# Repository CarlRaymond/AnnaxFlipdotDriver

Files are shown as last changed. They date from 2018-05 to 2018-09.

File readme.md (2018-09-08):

# Annax Flipdot Driver #

This is a driver for Annax flipdot display panels, with an Arduino nano or ESP8266 (Wemos D1 Mini) controller.

The controller consists of a row driver PC board, which contains the microcontroller,
and a column driver PC board. A span of panels can be any length. One row driver daisy
chains to all the panels, and each panel has its own column driver. The row and column
driver boards are connected together with a serial interface.

The row board acts as the master controller, and holds either an Arduino Nano or a WeMos D1 Mini
module.

The Nano has enough GPIO pins to supprt off-board connections to external controls,
supporting interactive applications. 

The WeMos D1 Mini is an ESP8266 device, with built-in WiFi capability. This allows using
the panel for signage, with remote configuration capability.

## Row Board ##
[Row board schematic](kicad/row_board/pdf/row_driver_schematic.pdf)
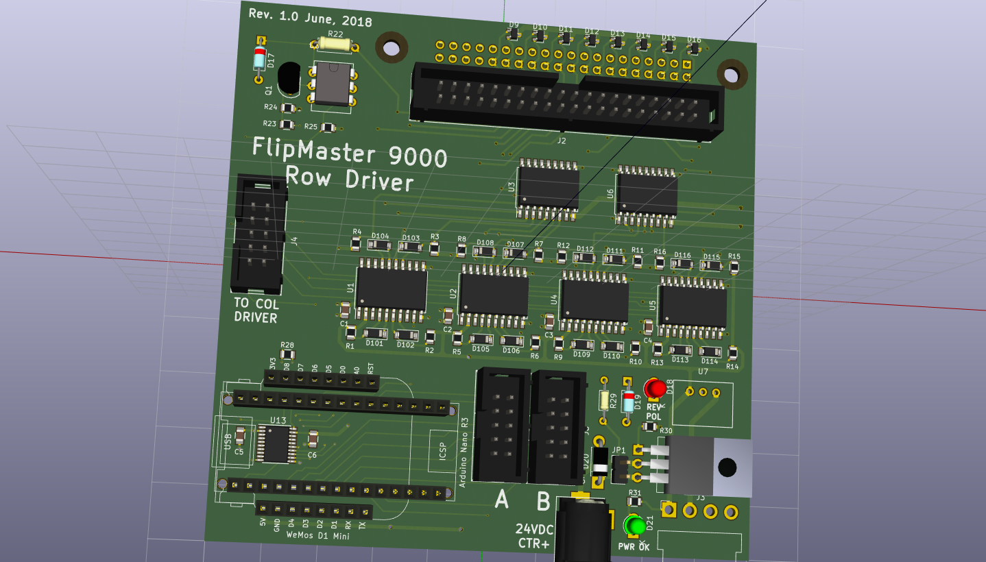
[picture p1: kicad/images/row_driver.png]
Image of row board


## Column Board ##
[Column board schematic](kicad/column_board/pdf/column_driver_schematic.pdf)
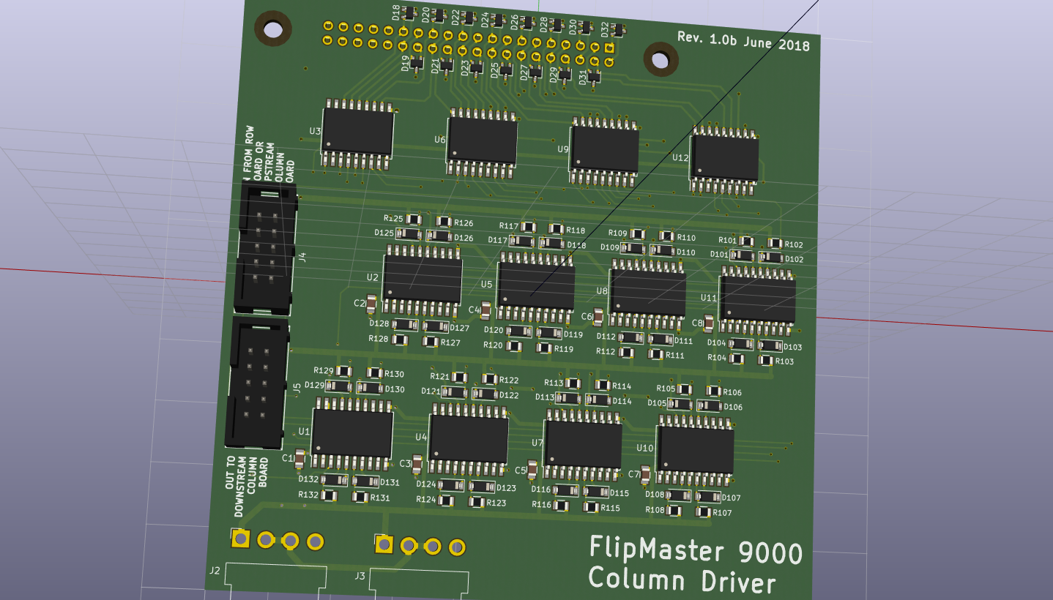
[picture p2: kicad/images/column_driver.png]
Image of column board


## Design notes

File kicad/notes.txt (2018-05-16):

Startup sequence:

At startup, all GPIO lines will be in input mode; /COL_ENABLE and /ROW_ENABLE will
be pulled high, diabling the row and column lines. The low-side lines coming out of
the shift registers will be inactive, but the high-side lines have pullups going into
the high side drivers. Both row and column high-side drivers will be active. No current
will flow in the coils.

The column driver boards have 32 lines coming from the shift registers.
Since the panels the boards are plugged into come in varying sizes
(20, 25, and 30 columns at least), and can be daisy-chained together in any
order, the first task is to determine how many columns there are in all, and
then determine where the "empty" positions are.

At startup, both the column and row drivers are all in the high-side active state. The
first step is to turn off all the row drivers (neither high or low side active). Do
this by shifting out 16 pairs of 0 followed by 1. The 0 turns off the low side drive
(making it float) and the 1 pulls down the corresponding bit in the shift register,
which turns off the high side drive. As long as any column driver is high, the column
presence sense line /SENSE will be active (driven low). We count the total columns by
shifting bits to turn off columns one by one until /SENSE goes high, indicating no more
columns are active.

Now we can determine the column positions by turning on the column high side drivers
one at a time, and checking the /SENSE line. This involves initially shifting in two
bits (00) to disable the low driver and enable the high driver of the first column, and
checking the sense line. Then shift out a (0, 1) pair to deactivate the first column
and activate the next. Repeat for each remaining column, whose number was determined
above.

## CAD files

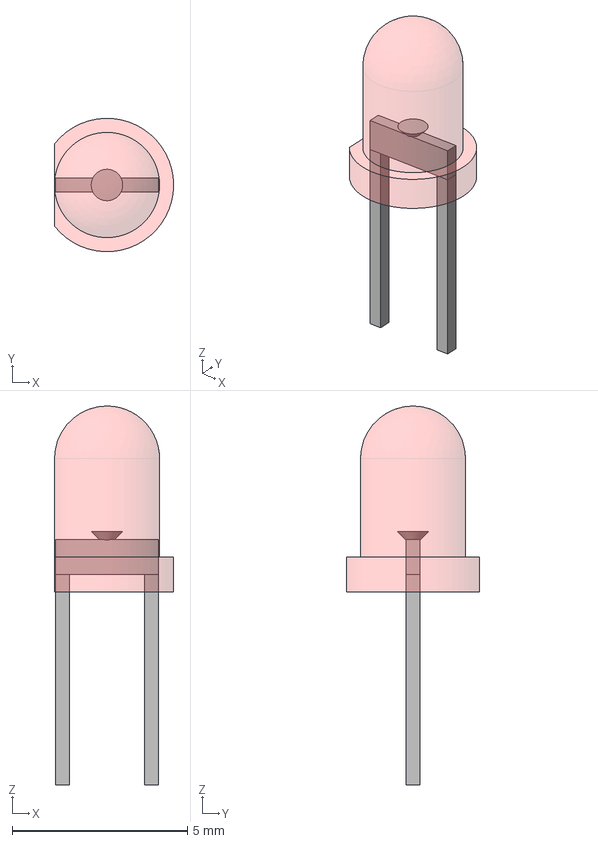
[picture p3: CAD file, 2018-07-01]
kicad/3d_models/LED_D3.0mm.FCStd
3.40 x 3.80 x 10.8 mm

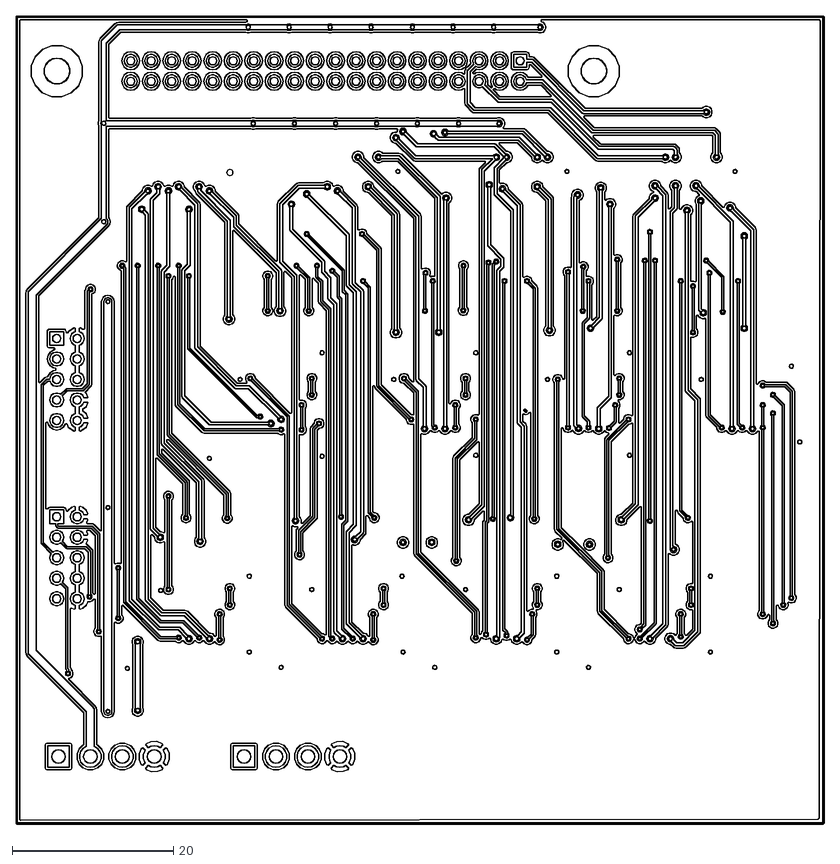
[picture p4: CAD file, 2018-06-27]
kicad/column_board/dxf/column_driver-B.Cu.dxf
100.2 x 100.2

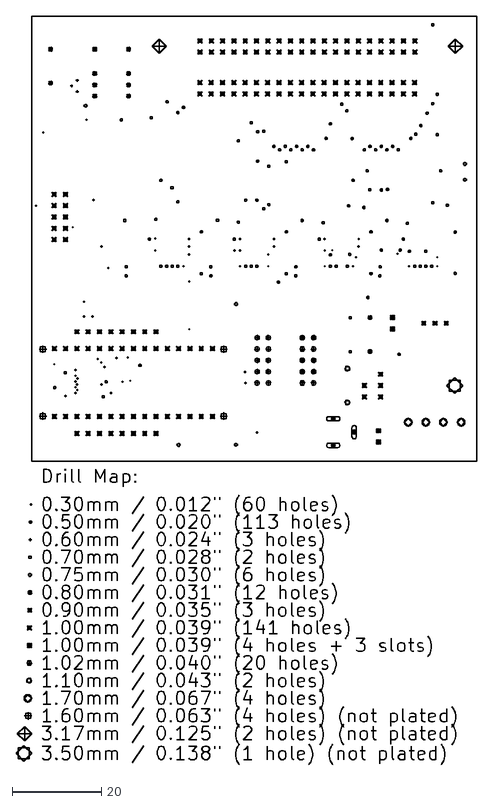
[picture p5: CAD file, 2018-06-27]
kicad/row_board/dxf/row_driver-drl_map.dxf
103.6 x 168.1

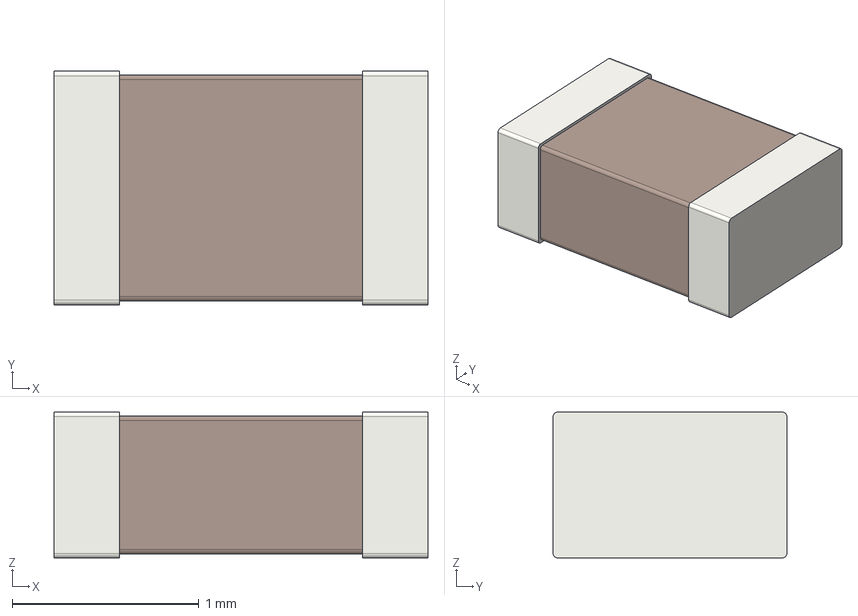
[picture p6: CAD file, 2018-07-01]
kicad/3d_models/C_0805.step
2.00 x 1.25 x 0.78 mm

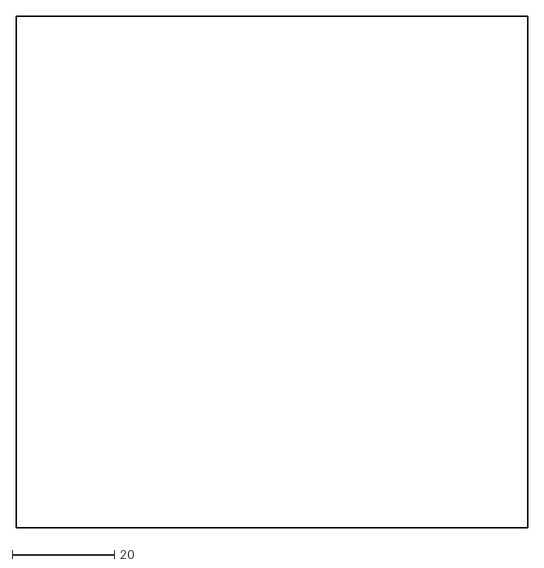
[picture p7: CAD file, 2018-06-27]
kicad/column_board/dxf/column_driver-Edge.Cuts.dxf
100.0 x 100.0

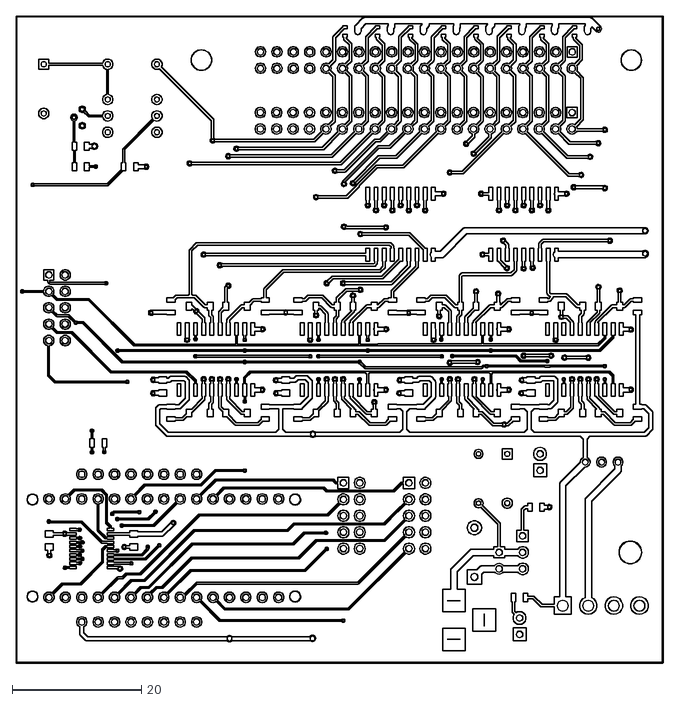
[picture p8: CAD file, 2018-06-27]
kicad/row_board/dxf/row_driver-F.Cu.dxf
100.2 x 100.2

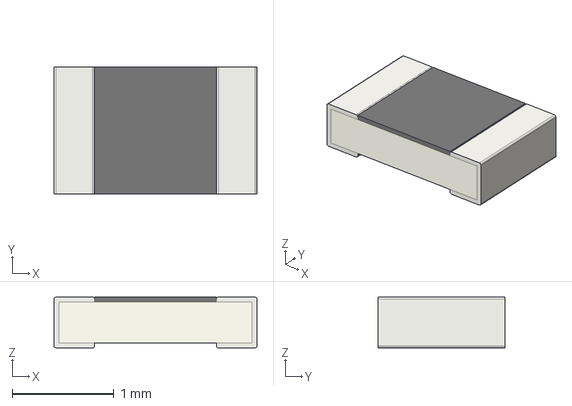
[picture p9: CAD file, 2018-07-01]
kicad/3d_models/R_0805.step
2.00 x 1.25 x 0.5 mm

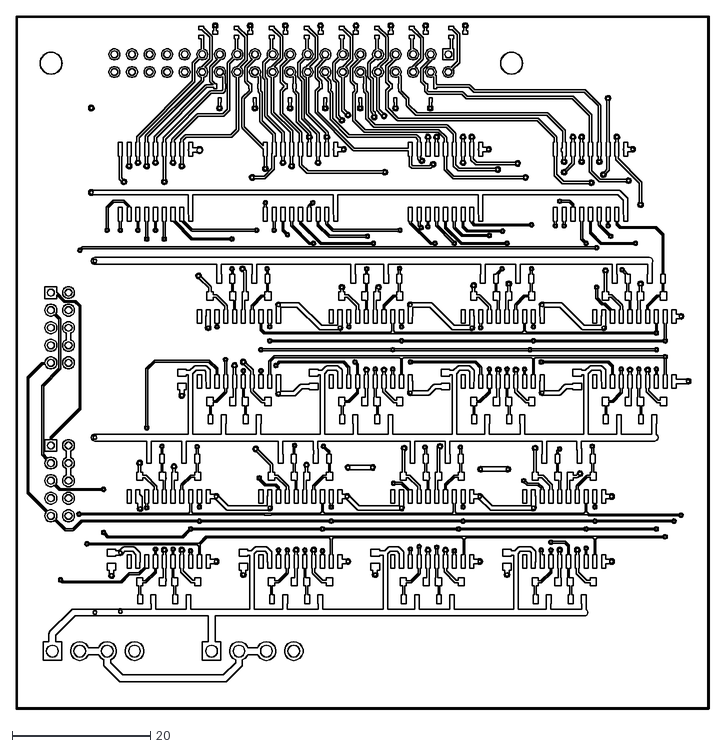
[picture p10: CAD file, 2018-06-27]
kicad/column_board/dxf/column_driver-F.Cu.dxf
100.2 x 100.2

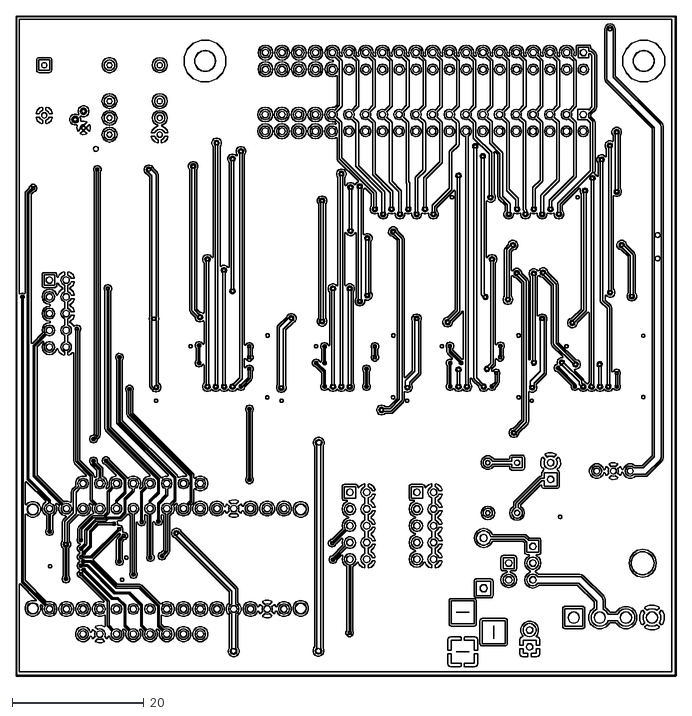
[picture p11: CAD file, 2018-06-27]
kicad/row_board/dxf/row_driver-B.Cu.dxf
100.2 x 100.2

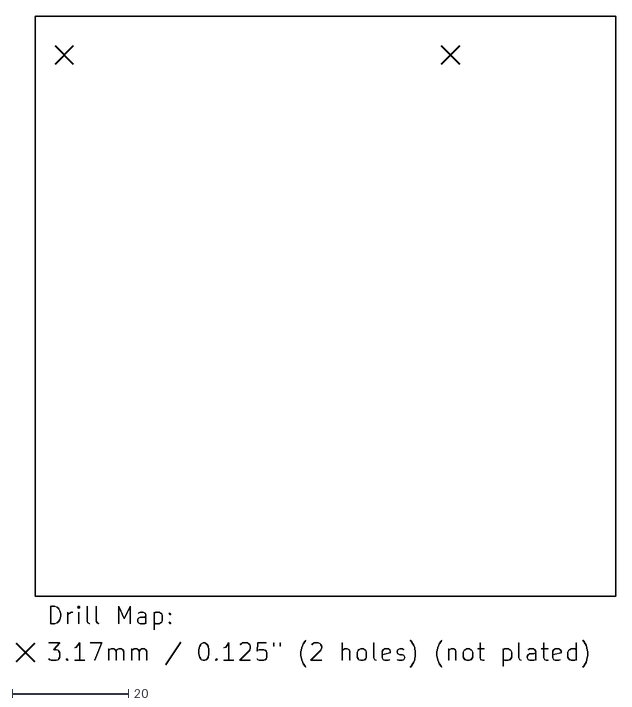
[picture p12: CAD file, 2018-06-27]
kicad/column_board/dxf/column_driver-NPTH-drl_map.dxf
103.2 x 112.2

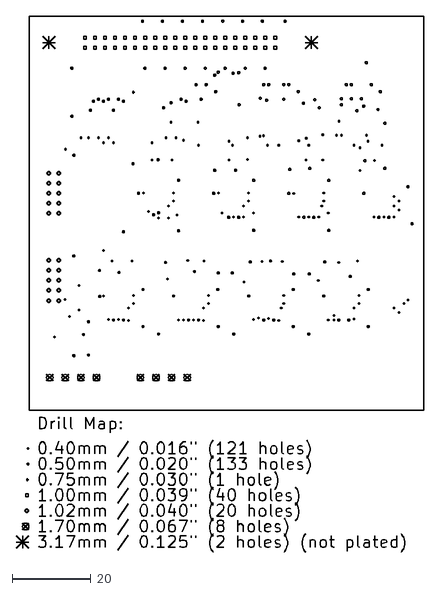
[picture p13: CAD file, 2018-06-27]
kicad/column_board/dxf/column_driver-drl_map.dxf
103.2 x 135.9

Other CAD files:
kicad/column_board/dxf/column_driver-B.Mask.dxf
kicad/column_board/dxf/column_driver-B.SilkS.dxf
kicad/column_board/dxf/column_driver-F.Mask.dxf
kicad/column_board/dxf/column_driver-F.SilkS.dxf
kicad/row_board/dxf/row_driver-B.Mask.dxf
kicad/row_board/dxf/row_driver-B.SilkS.dxf
kicad/row_board/dxf/row_driver-F.Mask.dxf
kicad/row_board/dxf/row_driver-F.SilkS.dxf

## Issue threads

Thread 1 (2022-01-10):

Compatibility with Luminator display?

EdwardDeaver, 2022-01-10:
Hi,

This is incredible work. Do you know if your driver board will work with Luminator displays?

Like this https://www.ebay.com/itm/144216620709?hash=item2193fafea5:g:N0wAAOSwDvphTfJC

Or this https://www.ebay.com/itm/193406265045?hash=item2d07e966d5:g:k~gAAOSwfqJgx9sI

CarlRaymond, 2022-01-10:
Edward, it's not plug-compatible for sure. My panel has two connectors, and the project has a circuit board for each one. The Luminator panel has a single connector, and so won't work at that level. Electrically it may work fine, if the panel is constructed the same way, and the row and column lines are brought out to that connector, and it has the steering diodes on board. But that's not a sure thing. So I'm afraid it's no help with that board.

That's the problem with these things. They are quite rare now, and they're not all identical. I'd like to get a couple more panels like I have, but I can't find them. Good luck!

Closed 2022-01-10.

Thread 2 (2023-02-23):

Update Readme with known issues

Kowitzki, 2023-02-23:
Firstly, thank you very much for your work. The pcbs work like a charm.
Could you update the readme with a known issues section?

- Like you said in your video: The ROW_EN and COL_EN lines need 10k pullup resistors to 5V, so the coils will not be harmed on a reset of the microcontroller.
- I had a little trouble with my 10x25 boards. Because the SENSE line is at row 16, and my board has no row 16, it could not autodetect its parameters. Rerouting the SENSE line to row 1 did the trick for me.

Maybe you could also add a link to your video series.

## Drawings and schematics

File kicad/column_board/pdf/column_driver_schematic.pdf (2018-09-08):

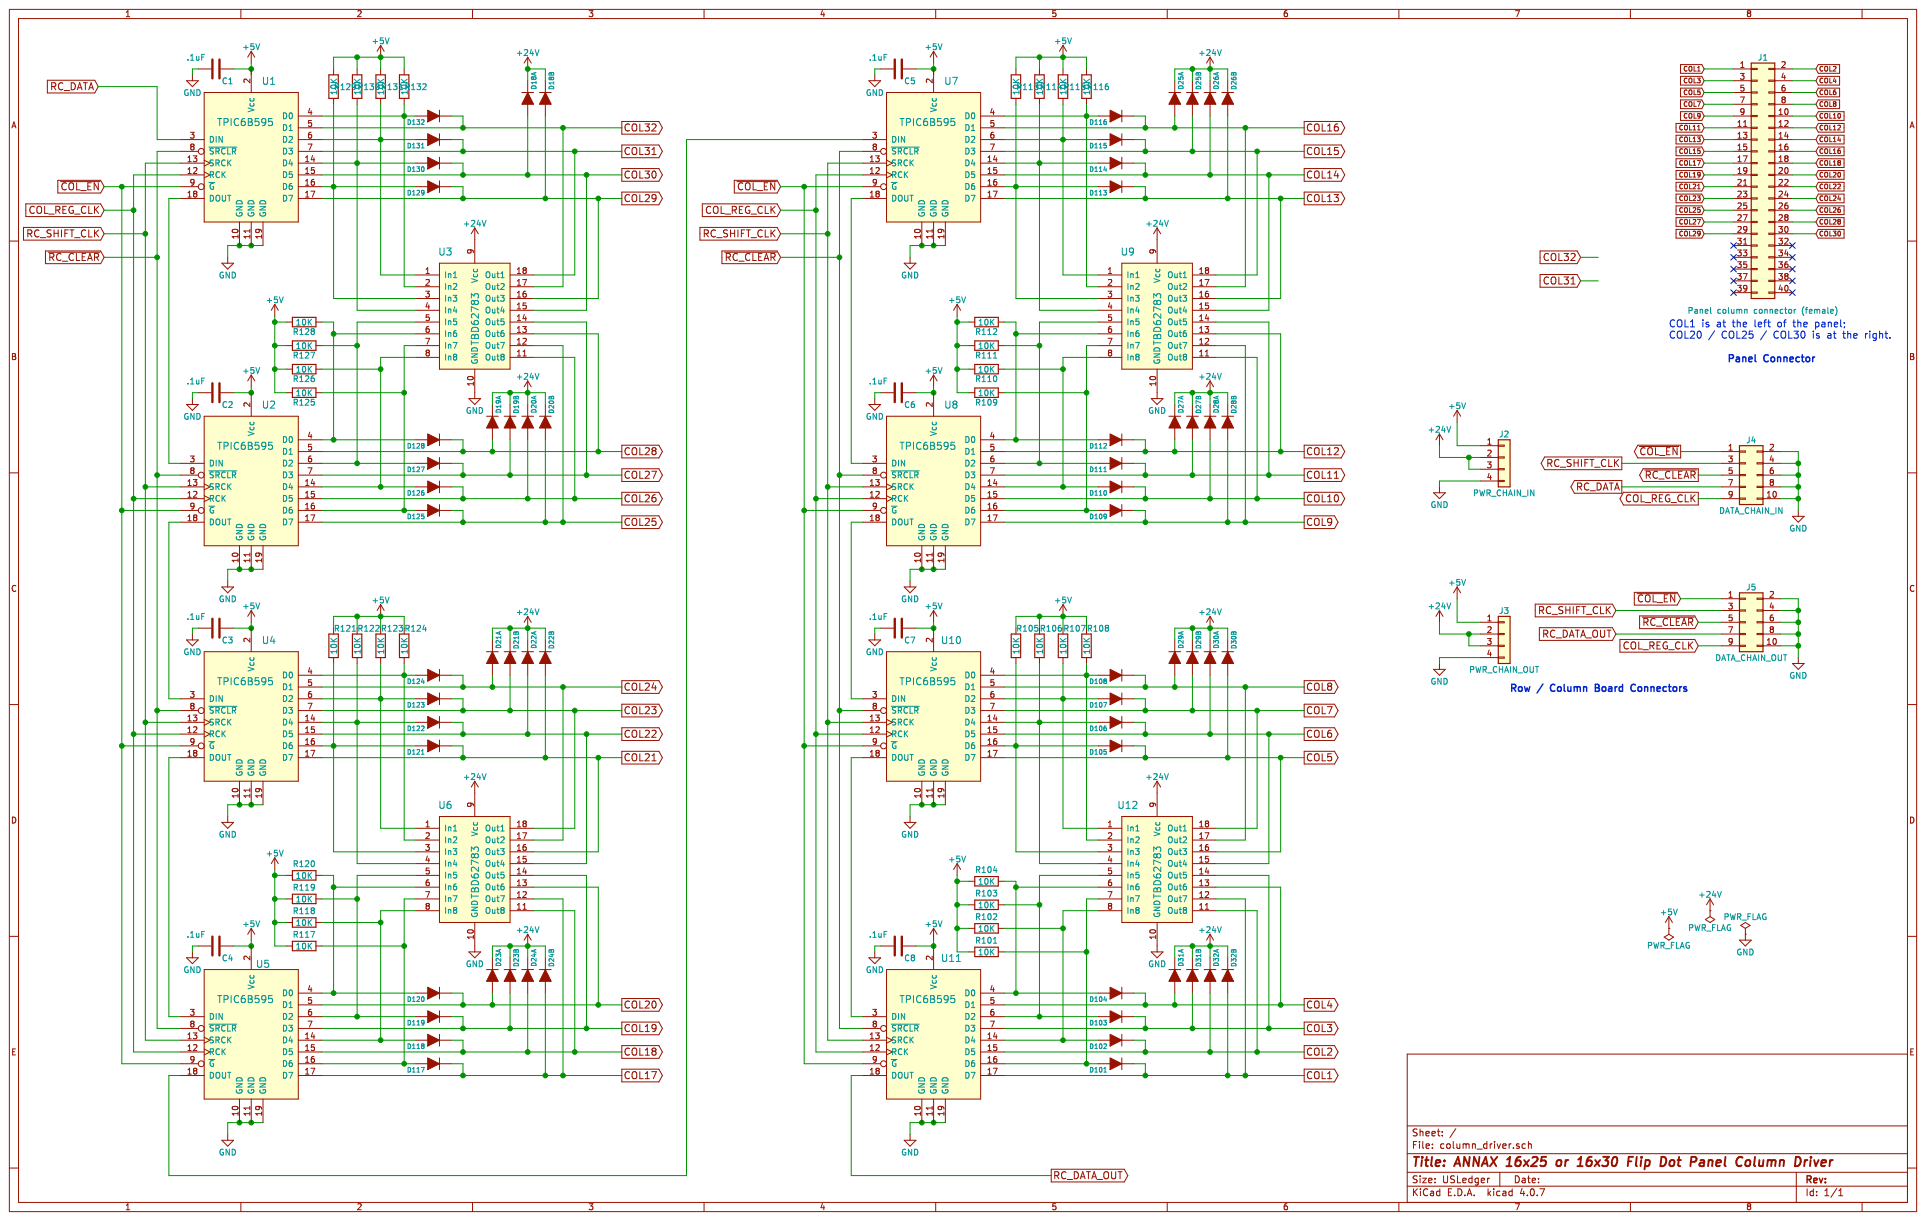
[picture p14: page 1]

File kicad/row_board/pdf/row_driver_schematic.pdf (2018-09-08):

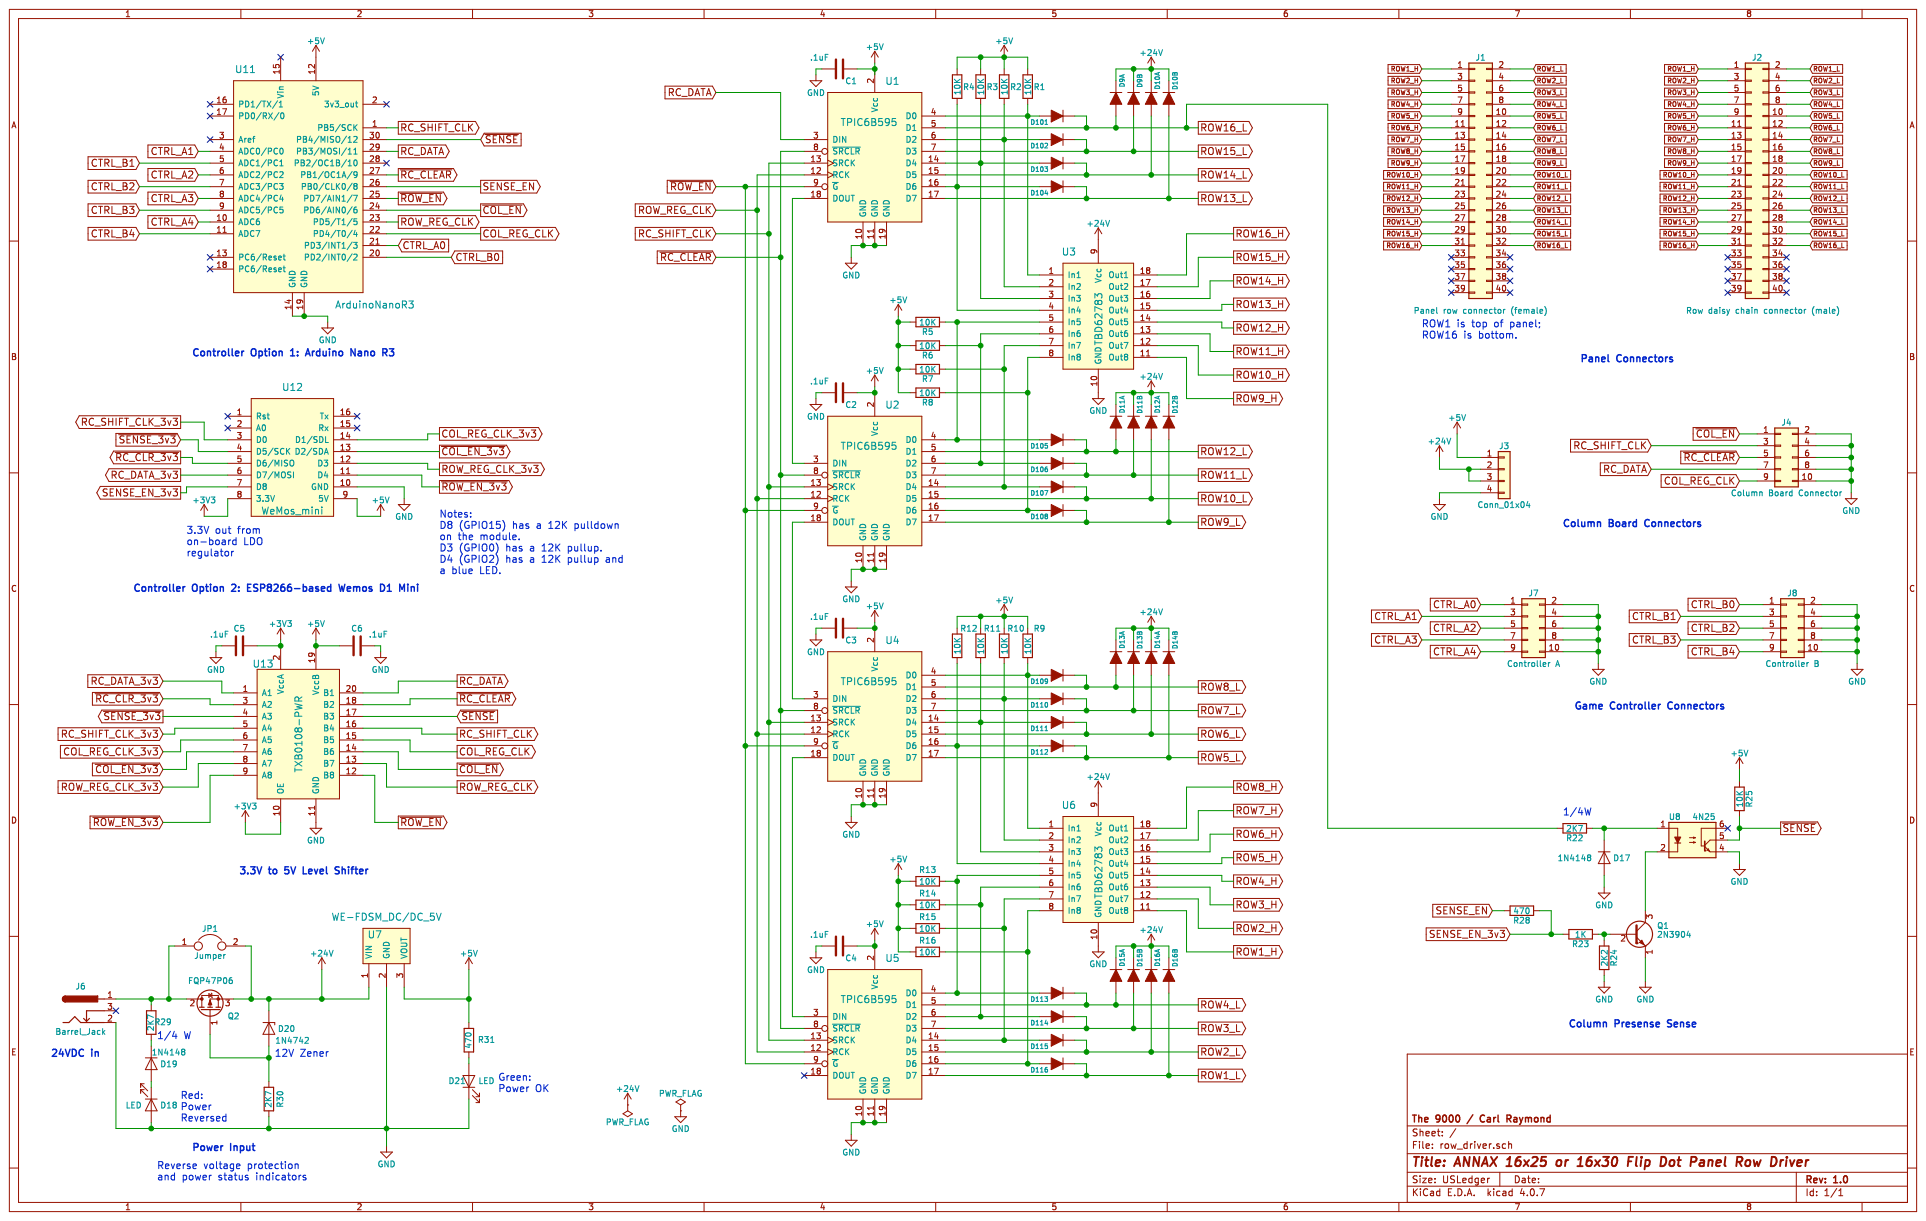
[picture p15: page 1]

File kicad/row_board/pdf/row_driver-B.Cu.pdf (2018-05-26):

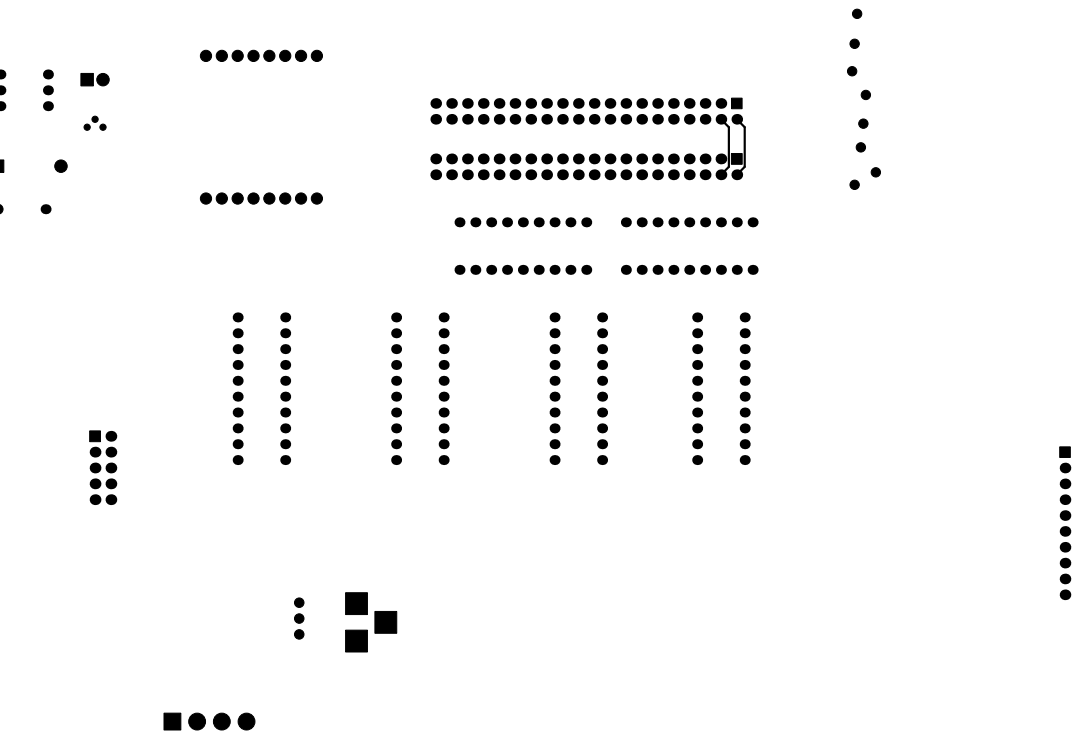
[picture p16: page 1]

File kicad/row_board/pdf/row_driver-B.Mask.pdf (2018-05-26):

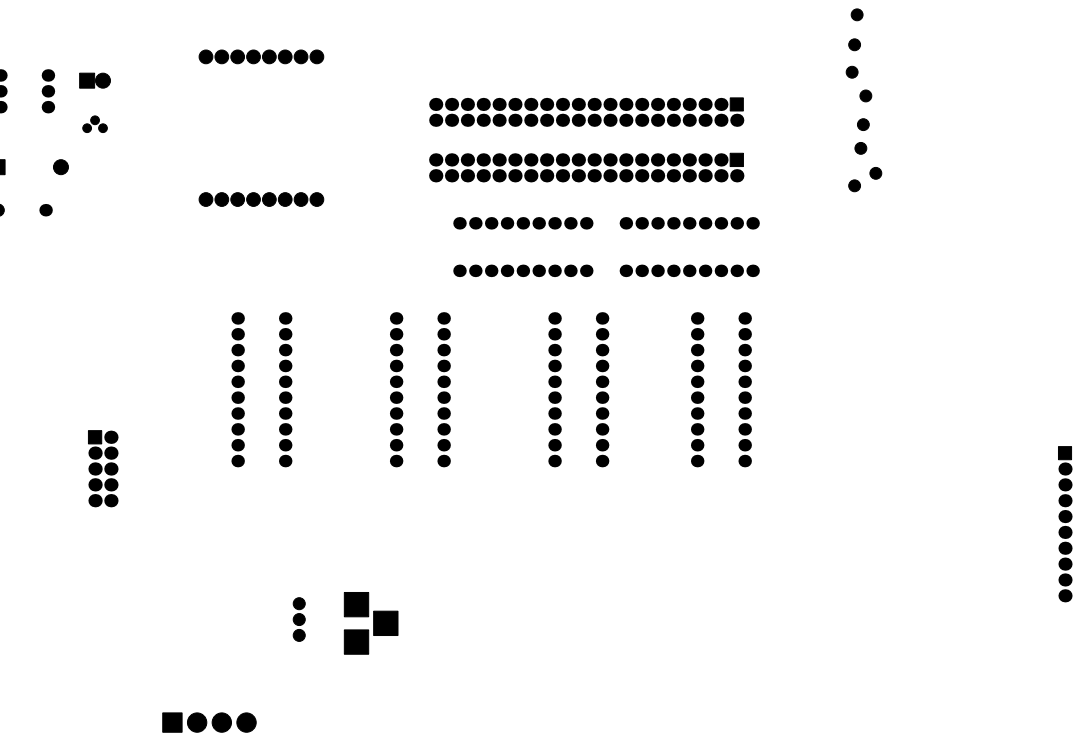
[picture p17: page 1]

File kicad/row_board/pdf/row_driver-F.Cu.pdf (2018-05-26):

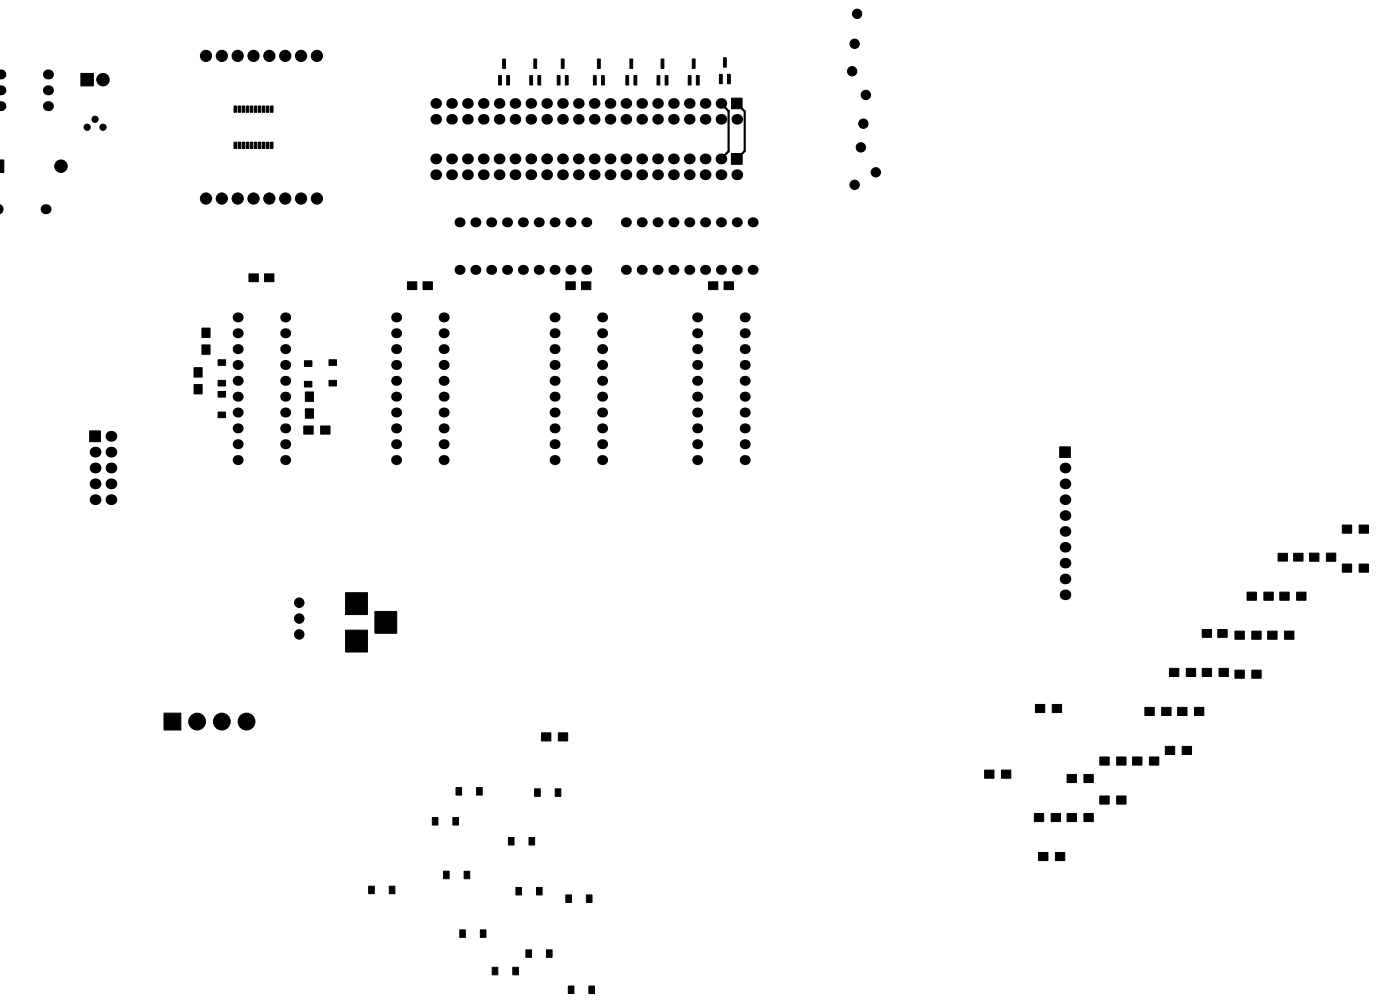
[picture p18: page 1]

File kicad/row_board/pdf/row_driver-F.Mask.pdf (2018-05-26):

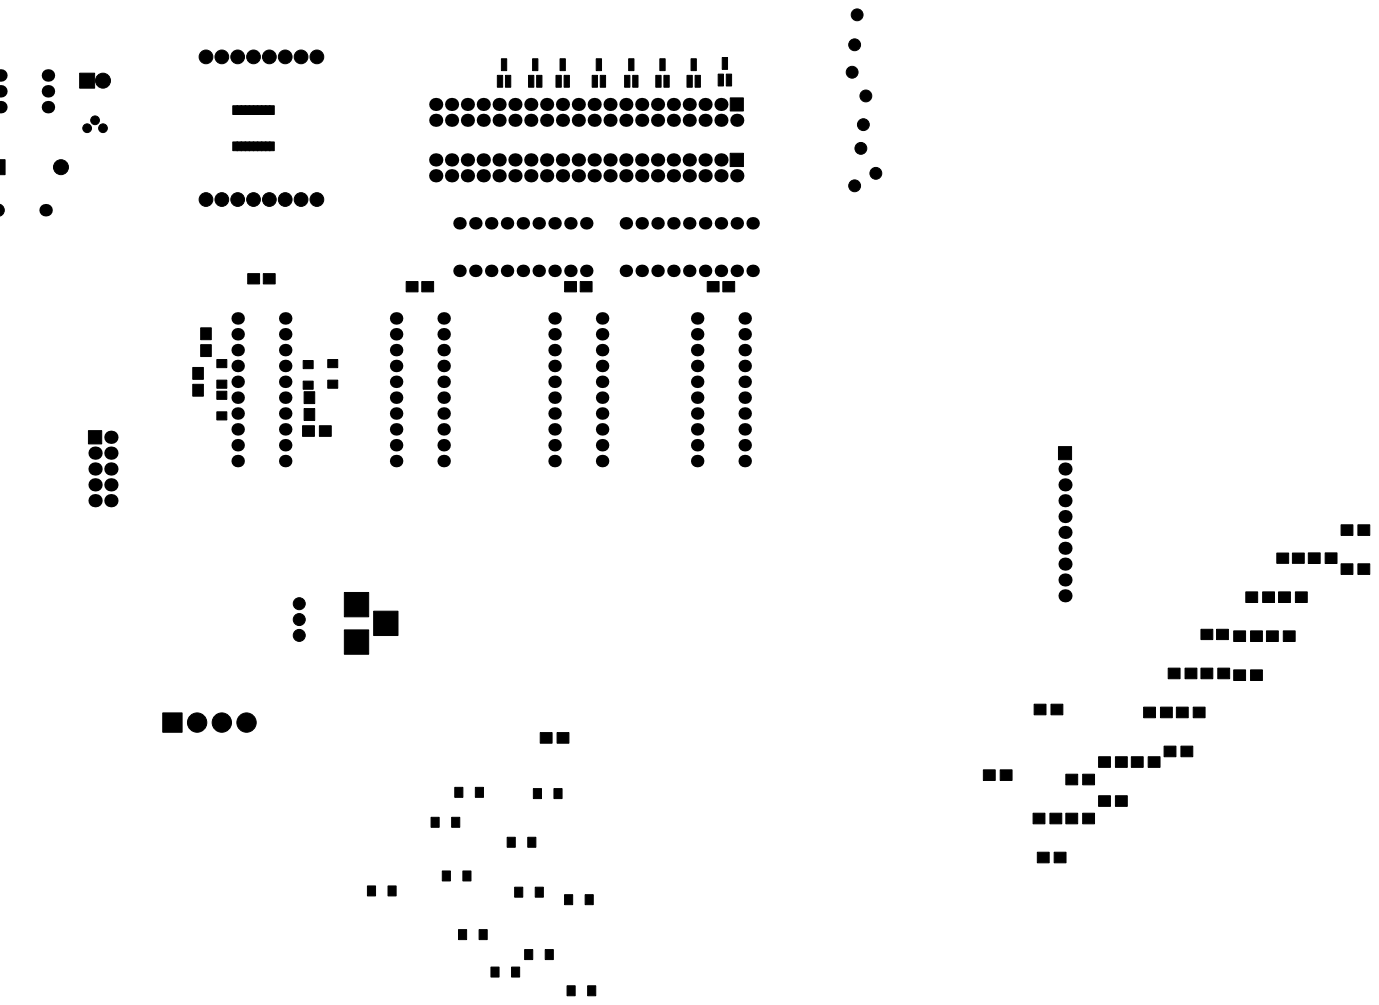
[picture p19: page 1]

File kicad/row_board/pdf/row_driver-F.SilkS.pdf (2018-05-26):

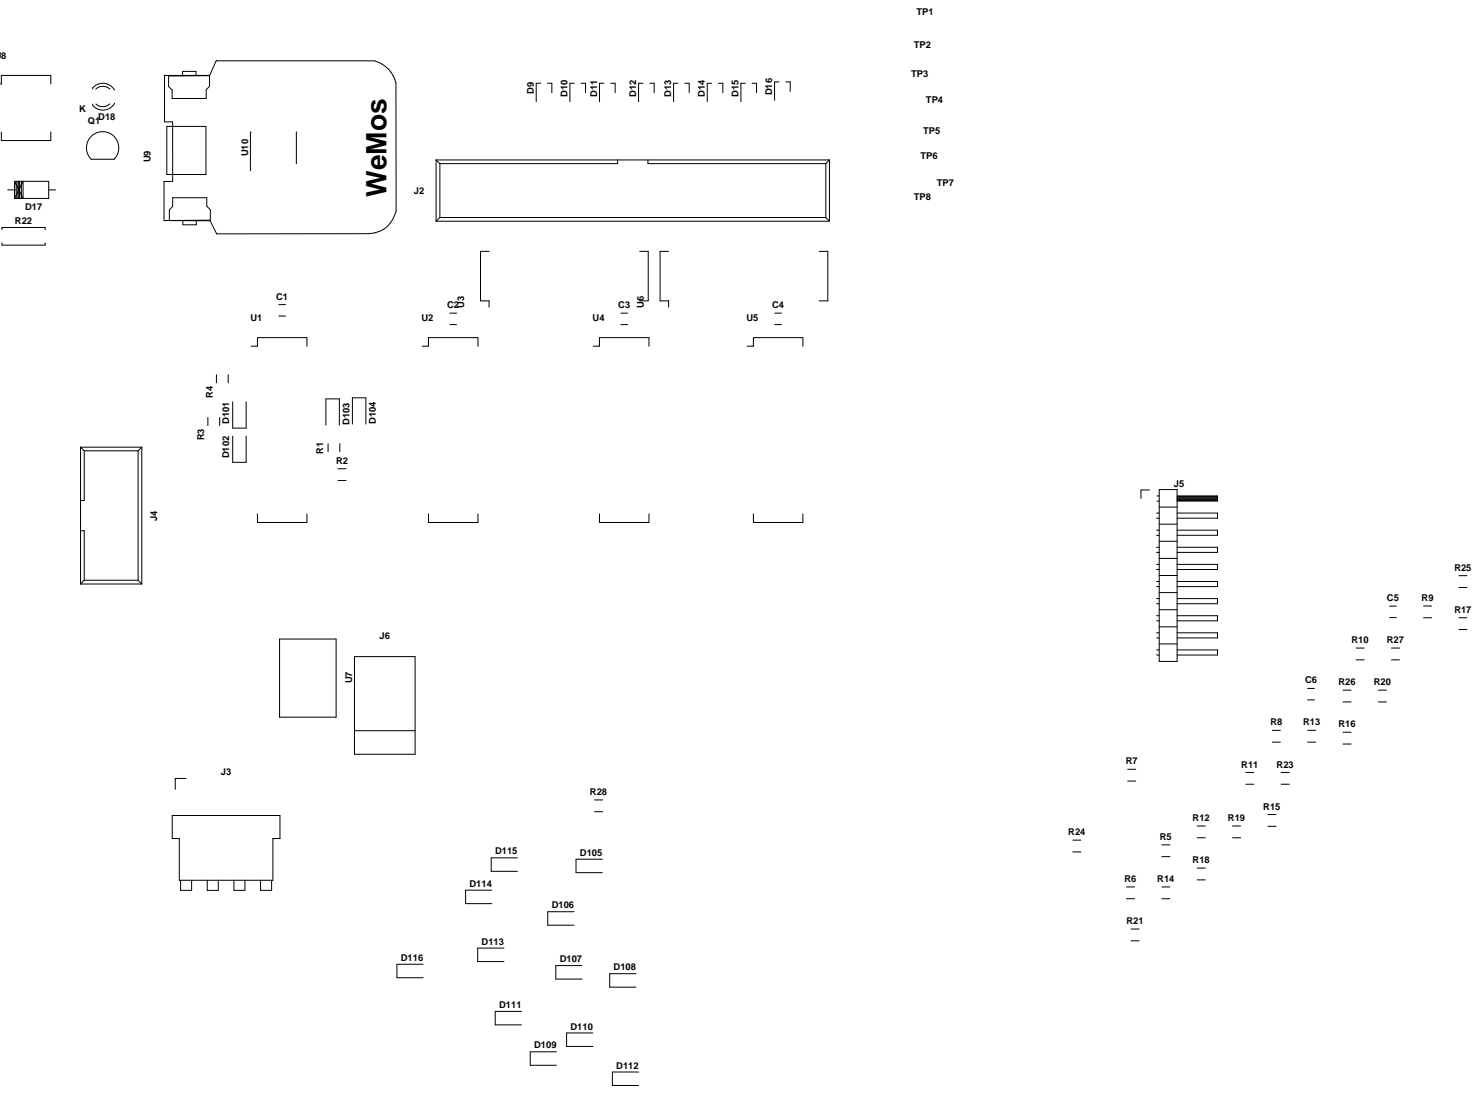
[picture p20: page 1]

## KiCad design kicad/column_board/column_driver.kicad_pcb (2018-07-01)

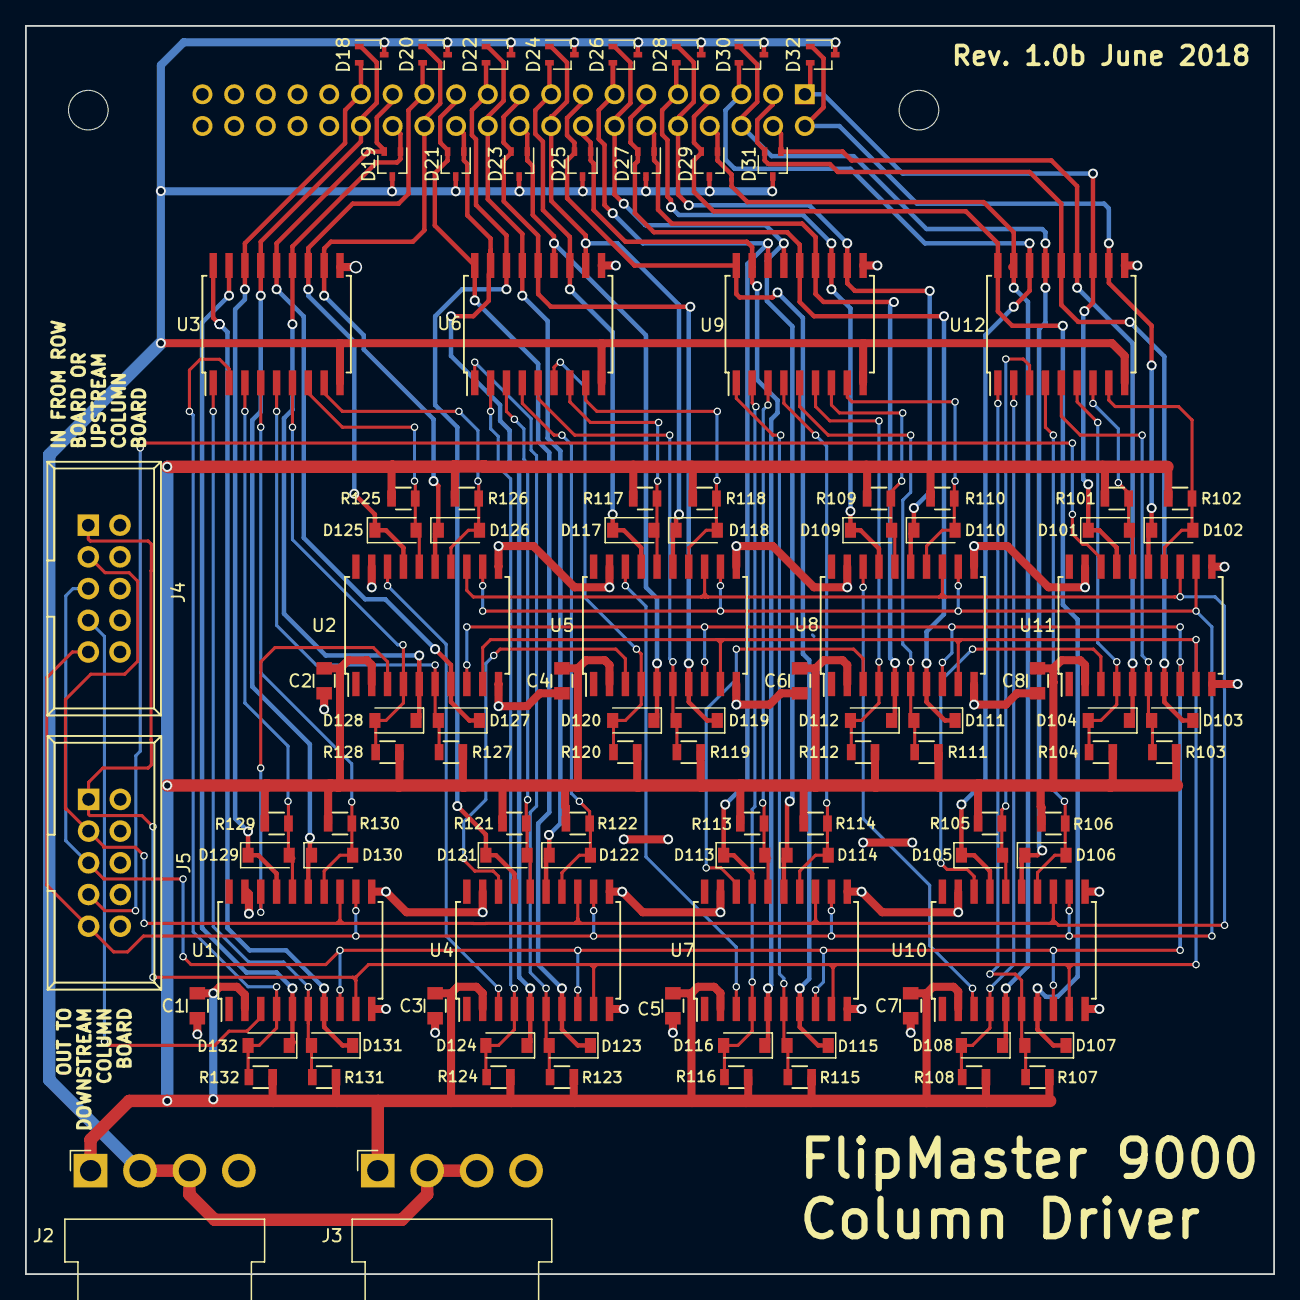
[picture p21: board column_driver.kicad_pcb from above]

Board: 2 copper layers, 100.0 x 100.0 mm, 104 parts (1 on the bottom side), 80 nets.

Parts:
C1, C2, C3, C4, C5, C6, C7, C8: .1uF; C_0805
D18, D19, D20, D21, D22, D23, D24, D25, D26, D27, D28, D29, D30, D31, D32: BAV70W; SOT-323_SC-70
D101, D102, D103, D104, D105, D106, D107, D108, D109, D110, D111, D112, D113, D114, D115, D116, D117, D118, D119, D120, D121, D122, D123, D124, D125, D126, D127, D128, D129, D130, D131, D132: BAS16GW; D_SOD-123
J1: Panel column connector (female); Socket_Strip_Straight_2x20_Pitch2.54mm
J2: PWR_CHAIN_IN; JST_VH_B4PS-VH_1x04_P3.96mm_Horizontal
J3: PWR_CHAIN_OUT; JST_VH_B4PS-VH_1x04_P3.96mm_Horizontal
J4: DATA_CHAIN_IN; IDC_Header_Straight_10pins
J5: DATA_CHAIN_OUT; IDC_Header_Straight_10pins
R101, R102, R103, R104, R105, R106, R107, R108, R109, R110, R111, R112, R113, R114, R115, R116, R117, R118, R119, R120, R121, R122, R123, R124, R125, R126, R127, R128, R129, R130, R131, R132: 10K; R_0805
U1, U2, U4, U5, U7, U8, U10, U11: TPIC6B595; SOIC-20W_7.5x12.8mm_Pitch1.27mm
U3, U6, U9, U12: TBD62783; SOIC-18W_7.5x11.6mm_Pitch1.27mm

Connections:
+5V: C1.1, C2.1, C3.1, C4.1, C5.1, C6.1, C7.1, C8.1, J2.1, J3.1, R101.2, R102.2, R103.1, R104.2, R105.1, R106.1, R107.1, R108.1, R109.2, R110.2, R111.2, R112.2, R113.1, R114.1, R115.1, R116.1, R117.2, R118.2, R119.1, R120.2, R121.1, R122.1, R123.1, R124.1, R125.2, R126.2, R127.2, R128.2, R129.1, R130.1, R131.1, R132.1, U1.2, U2.2, U4.2, U5.2, U7.2, U8.2, U10.2, U11.2
+24V: D18.3, D19.3, D20.3, D21.3, D22.3, D23.3, D24.3, D25.3, D26.3, D27.3, D28.3, D29.3, D30.3, D31.3, D32.3, J2.2, J2.3, J3.2, J3.3, U3.9, U6.9, U9.9, U12.9
COL1: D32.2, D101.1, J1.1, U11.17, U12.12
COL2: D32.1, D102.1, J1.2, U11.15, U12.11
COL3: D31.2, D103.1, J1.3, U11.7, U12.14
COL4: D31.1, D104.1, J1.4, U11.5, U12.13
COL5: D30.2, D105.1, J1.5, U10.17, U12.16
COL6: D30.1, D106.1, J1.6, U10.15, U12.15
COL7: D29.2, D107.1, J1.7, U10.7, U12.18
COL8: D29.1, D108.1, J1.8, U10.5, U12.17
COL9: D28.2, D109.1, J1.9, U8.17, U9.12
COL10: D28.1, D110.1, J1.10, U8.15, U9.11
COL11: D27.2, D111.1, J1.11, U8.7, U9.14
COL12: D27.1, D112.1, J1.12, U8.5, U9.13
COL13: D26.2, D113.1, J1.13, U7.17, U9.16
COL14: D26.1, D114.1, J1.14, U7.15, U9.15
COL15: D25.2, D115.1, J1.15, U7.7, U9.18
COL16: D25.1, D116.1, J1.16, U7.5, U9.17
COL17: D24.2, D117.1, J1.17, U5.17, U6.12
COL18: D24.1, D118.1, J1.18, U5.15, U6.11
COL19: D23.2, D119.1, J1.19, U5.7, U6.14
COL20: D23.1, D120.1, J1.20, U5.5, U6.13
COL21: D22.2, D121.1, J1.21, U4.17, U6.16
COL22: D22.1, D122.1, J1.22, U4.15, U6.15
COL23: D21.2, D123.1, J1.23, U4.7, U6.18
COL24: D21.1, D124.1, J1.24, U4.5, U6.17
COL25: D20.2, D125.1, J1.25, U2.17, U3.12
COL26: D20.1, D126.1, J1.26, U2.15, U3.11
COL27: D19.2, D127.1, J1.27, U2.7, U3.14
COL28: D19.1, D128.1, J1.28, U2.5, U3.13
COL29: D18.2, D129.1, J1.29, U1.17, U3.16
COL30: D18.1, D130.1, J1.30, U1.15, U3.15
COL31: D131.1, U1.7, U3.18
COL32: D132.1, U1.5, U3.17
COL_REG_CLK: J4.9, J5.9, U1.12, U2.12, U4.12, U5.12, U7.12, U8.12, U10.12, U11.12
GND: C1.2, C2.2, C3.2, C4.2, C5.2, C6.2, C7.2, C8.2, J2.4, J3.4, J4.2, J4.4, J4.6, J4.8, J4.10, J5.2, J5.4, J5.6, J5.8, J5.10, U1.10, U1.11, U1.19, U2.10, U2.11, U2.19, U3.10, U4.10, U4.11, U4.19, U5.10, U5.11, U5.19, U6.10, U7.10, U7.11, U7.19, U8.10, U8.11, U8.19, U9.10, U10.10, U10.11, U10.19, U11.10, U11.11, U11.19, U12.10
unnamed: D101.2, R101.1, U11.16, U12.7
unnamed: D102.2, R102.1, U11.14, U12.8
unnamed: D103.2, R103.2, U11.6, U12.5
unnamed: D104.2, R104.1, U11.4, U12.6
unnamed: D105.2, R105.2, U10.16, U12.3
unnamed: D106.2, R106.2, U10.14, U12.4
unnamed: D107.2, R107.2, U10.6, U12.1
unnamed: D108.2, R108.2, U10.4, U12.2
unnamed: D109.2, R109.1, U8.16, U9.7
unnamed: D110.2, R110.1, U8.14, U9.8
unnamed: D111.2, R111.1, U8.6, U9.5
unnamed: D112.2, R112.1, U8.4, U9.6
unnamed: D113.2, R113.2, U7.16, U9.3
unnamed: D114.2, R114.2, U7.14, U9.4
unnamed: D115.2, R115.2, U7.6, U9.1
unnamed: D116.2, R116.2, U7.4, U9.2
unnamed: D117.2, R117.1, U5.16, U6.7
unnamed: D118.2, R118.1, U5.14, U6.8
unnamed: D119.2, R119.2, U5.6, U6.5
unnamed: D120.2, R120.1, U5.4, U6.6
unnamed: D121.2, R121.2, U4.16, U6.3
unnamed: D122.2, R122.2, U4.14, U6.4
unnamed: D123.2, R123.2, U4.6, U6.1
unnamed: D124.2, R124.2, U4.4, U6.2
unnamed: D125.2, R125.1, U2.16, U3.7
unnamed: D126.2, R126.1, U2.14, U3.8
unnamed: D127.2, R127.1, U2.6, U3.5
unnamed: D128.2, R128.1, U2.4, U3.6
unnamed: D129.2, R129.2, U1.16, U3.3
unnamed: D130.2, R130.2, U1.14, U3.4
unnamed: D131.2, R131.2, U1.6, U3.1
unnamed: D132.2, R132.2, U1.4, U3.2
unnamed: U1.18, U2.3
unnamed: U2.18, U4.3
unnamed: U4.18, U5.3
unnamed: U5.18, U7.3
unnamed: U7.18, U8.3
unnamed: U8.18, U10.3
unnamed: U10.18, U11.3
RC_DATA: J4.7, U1.3
RC_DATA_OUT: J5.7, U11.18
RC_SHIFT_CLK: J4.3, J5.3, U1.13, U2.13, U4.13, U5.13, U7.13, U8.13, U10.13, U11.13
~COL_EN: J4.1, J5.1, U1.9, U2.9, U4.9, U5.9, U7.9, U8.9, U10.9, U11.9
~RC_CLEAR: J4.5, J5.5, U1.8, U2.8, U4.8, U5.8, U7.8, U8.8, U10.8, U11.8

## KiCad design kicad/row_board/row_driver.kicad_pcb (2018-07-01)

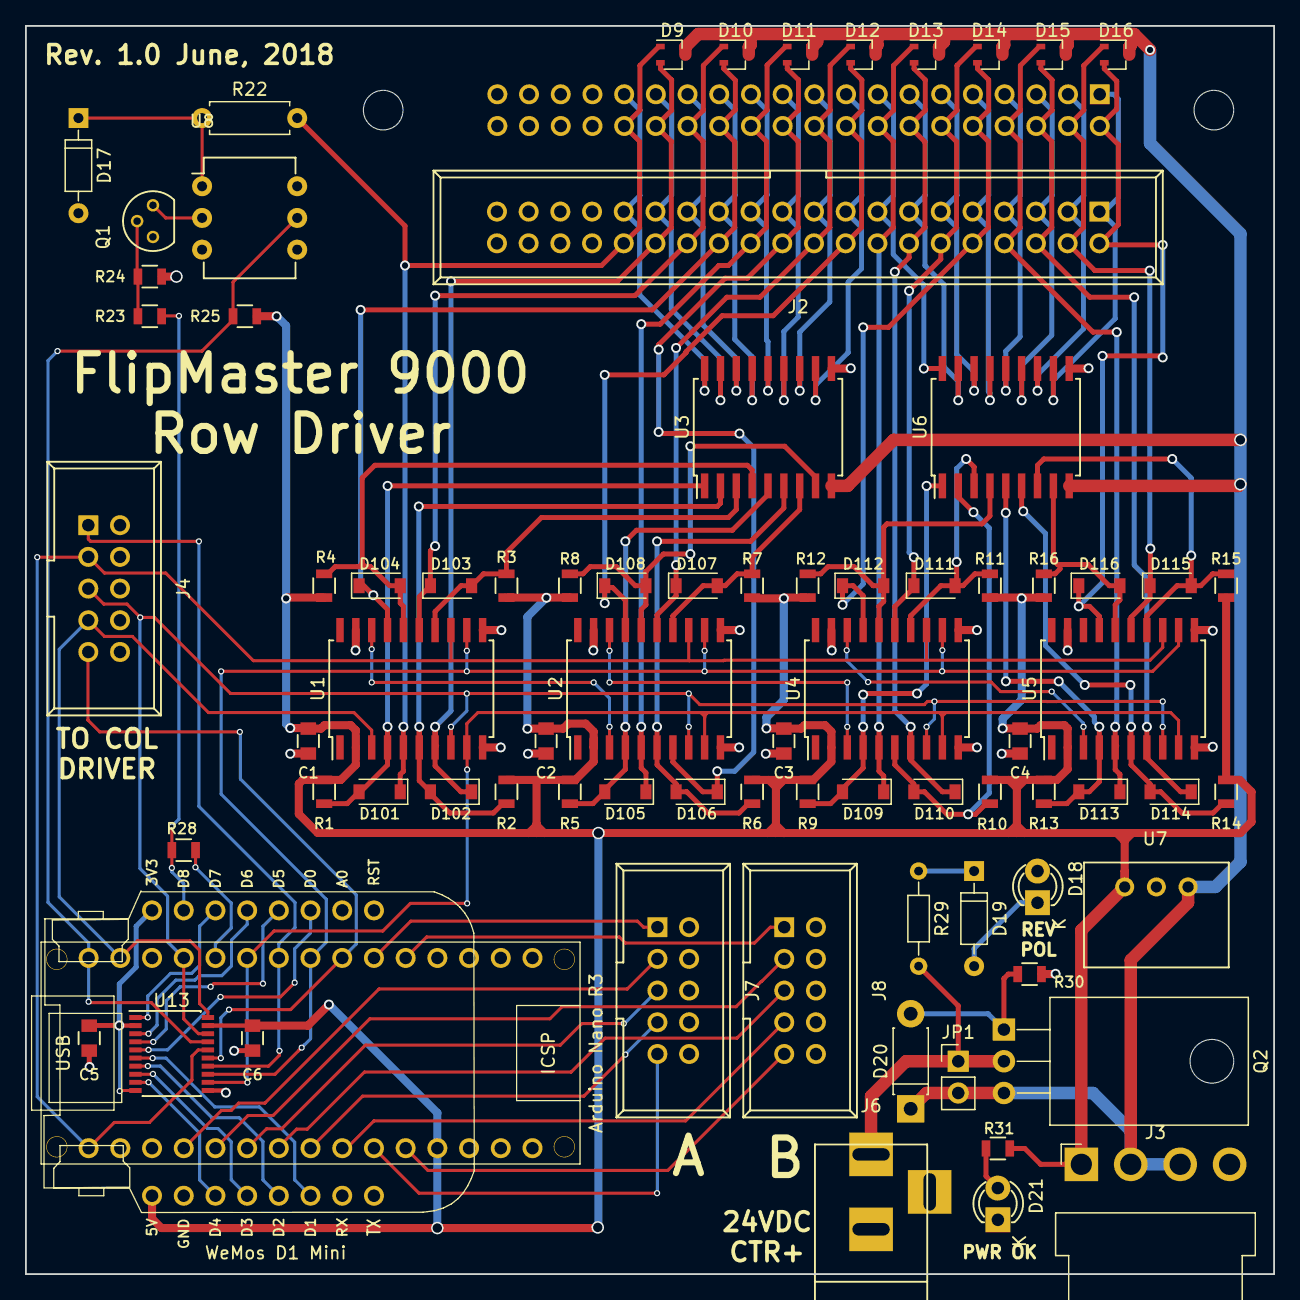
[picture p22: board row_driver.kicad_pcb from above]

Board: 2 copper layers, 100.0 x 100.0 mm, 80 parts (1 on the bottom side), 91 nets.

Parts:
C1, C2, C3, C4, C5, C6: .1uF; C_0805
D9, D10, D11, D12, D13, D14, D15, D16: BAV70W; SOT-323_SC-70
D17, D19: 1N4148; D_DO-35_SOD27_P7.62mm_Horizontal
D18, D21: LED; LED-3MM
D20: 1N4742; D_DO-41_SOD81_P7.62mm_Horizontal
D101, D102, D103, D104, D105, D106, D107, D108, D109, D110, D111, D112, D113, D114, D115, D116: BAS16GW; D_SOD-123
J1: Panel row connector (female); Socket_Strip_Straight_2x20_Pitch2.54mm
J2: Row daisy chain connector (male); IDC_Header_Straight_40pins
J3: Conn_01x04; JST_VH_B4PS-VH_1x04_P3.96mm_Horizontal
J4: Column Board Connector; IDC_Header_Straight_10pins
J6: Barrel_Jack; BARREL_JACK
J7: Controller A; IDC_Header_Straight_10pins
J8: Controller B; IDC_Header_Straight_10pins
JP1: Jumper; Pin_Header_Straight_1x02_Pitch2.54mm
Q1: 2N3904; TO-92_Molded_Narrow
Q2: FQP47P06; TO-220_Horizontal
R1, R2, R3, R4, R5, R6, R7, R8, R9, R10, R11, R12, R13, R14, R15, R16, R25: 10K; R_0805
R22: 2K7; R_Axial_DIN0207_L6.3mm_D2.5mm_P7.62mm_Horizontal
R23: 1K; R_0805
R24: 2K2; R_0805
R28, R31: 470; R_0805
R29: 2K7; R_Axial_DIN0204_L3.6mm_D1.6mm_P7.62mm_Horizontal
R30: 2K7; R_0805
U1, U2, U4, U5: TPIC6B595; SOIC-20W_7.5x12.8mm_Pitch1.27mm
U3, U6: TBD62783; SOIC-18W_7.5x11.6mm_Pitch1.27mm
U7: WE-FDSM_DC/DC_5V; WPMDL9500xx
U8: 4N25; DIP-6_W7.62mm
U11: ArduinoNanoR3; Arduino_Nano_R3
U12: WeMos_mini; D1_mini_can_up
U13: TXB0108-PWR; SSOP-20_4.4x6.5mm_Pitch0.65mm

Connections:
+3V3: C5.1, U12.8, U13.2, U13.10
+5V: C1.1, C2.1, C3.1, C4.1, C6.2, J3.1, R1.1, R2.1, R3.1, R4.1, R5.2, R6.2, R7.2, R8.2, R9.1, R10.1, R11.1, R12.1, R13.2, R14.1, R15.2, R16.2, R25.1, R31.2, U1.2, U2.2, U4.2, U5.2, U7.3, U11.12, U12.9, U13.19
+24V: D9.3, D10.3, D11.3, D12.3, D13.3, D14.3, D15.3, D16.3, D20.1, J3.2, J3.3, JP1.2, Q2.3, U3.9, U6.9, U7.1
COL_REG_CLK: J4.9, U11.22, U13.15
COL_REG_CLK_3v3: U12.14, U13.6
CTRL_A0: J7.1, U11.21
CTRL_A1: J7.3, U11.4
CTRL_A2: J7.5, U11.6
CTRL_A3: J7.7, U11.8
CTRL_A4: J7.9, U11.10
CTRL_B0: J8.1, U11.20
CTRL_B1: J8.3, U11.5
CTRL_B2: J8.5, U11.7
CTRL_B3: J8.7, U11.9
CTRL_B4: J8.9, U11.11
GND: C1.2, C2.2, C3.2, C4.2, C5.2, C6.1, D17.2, D18.2, D21.1, J3.4, J4.2, J4.4, J4.6, J4.8, J4.10, J6.2, J7.2, J7.4, J7.6, J7.8, J7.10, J8.2, J8.4, J8.6, J8.8, J8.10, Q1.1, R24.2, R30.1, U1.10, U1.11, U1.19, U2.10, U2.11, U2.19, U3.10, U4.10, U4.11, U4.19, U5.10, U5.11, U5.19, U6.10, U7.2, U8.4, U11.14, U11.19, U12.10, U13.11
unnamed: D17.1, R22.1, U8.1
unnamed: D18.1, D19.2
unnamed: D19.1, R29.1
unnamed: D20.2, Q2.1, R30.2
unnamed: D21.2, R31.1
unnamed: D101.2, R1.2, U1.4, U3.1
unnamed: D102.2, R2.2, U1.6, U3.2
unnamed: D103.2, R3.2, U1.14, U3.3
unnamed: D104.2, R4.2, U1.16, U3.4
unnamed: D105.2, R5.1, U2.4, U3.5
unnamed: D106.2, R6.1, U2.6, U3.6
unnamed: D107.2, R7.1, U2.14, U3.7
unnamed: D108.2, R8.1, U2.16, U3.8
unnamed: D109.2, R9.2, U4.4, U6.1
unnamed: D110.2, R10.2, U4.6, U6.2
unnamed: D111.2, R11.2, U4.14, U6.3
unnamed: D112.2, R12.2, U4.16, U6.4
unnamed: D113.2, R13.1, U5.4, U6.5
unnamed: D114.2, R14.2, U5.6, U6.6
unnamed: D115.2, R15.1, U5.14, U6.7
unnamed: D116.2, R16.1, U5.16, U6.8
unnamed: J6.1, JP1.1, Q2.2, R29.2
unnamed: Q1.2, R23.1, R24.1
unnamed: Q1.3, U8.2
unnamed: U1.18, U2.3
unnamed: U2.18, U4.3
unnamed: U4.18, U5.3
RC_DATA: J4.7, U1.3, U11.29, U13.20
RC_DATA_3v3: U12.6, U13.1
RC_SHIFT_CLK: J4.3, U1.13, U2.13, U4.13, U5.13, U11.1, U13.16
RC_SHIFT_CLK_3v3: U12.3, U13.5
ROW1_H: J1.1, J2.1, U6.11
ROW1_L: D16.2, D116.1, J1.2, J2.2, U5.17
ROW2_H: J1.3, J2.3, U6.12
ROW2_L: D16.1, D115.1, J1.4, J2.4, U5.15
ROW3_H: J1.5, J2.5, U6.13
ROW3_L: D15.2, D114.1, J1.6, J2.6, U5.7
ROW4_H: J1.7, J2.7, U6.14
ROW4_L: D15.1, D113.1, J1.8, J2.8, U5.5
ROW5_H: J1.9, J2.9, U6.15
ROW5_L: D14.2, D112.1, J1.10, J2.10, U4.17
ROW6_H: J1.11, J2.11, U6.16
ROW6_L: D14.1, D111.1, J1.12, J2.12, U4.15
ROW7_H: J1.13, J2.13, U6.17
ROW7_L: D13.2, D110.1, J1.14, J2.14, U4.7
ROW8_H: J1.15, J2.15, U6.18
ROW8_L: D13.1, D109.1, J1.16, J2.16, U4.5
ROW9_H: J1.17, J2.17, U3.11
ROW9_L: D12.2, D108.1, J1.18, J2.18, U2.17
ROW10_H: J1.19, J2.19, U3.12
ROW10_L: D12.1, D107.1, J1.20, J2.20, U2.15
ROW11_H: J1.21, J2.21, U3.13
ROW11_L: D11.2, D106.1, J1.22, J2.22, U2.7
ROW12_H: J1.23, J2.23, U3.14
ROW12_L: D11.1, D105.1, J1.24, J2.24, U2.5
ROW13_H: J1.25, J2.25, U3.15
ROW13_L: D10.2, D104.1, J1.26, J2.26, U1.17
ROW14_H: J1.27, J2.27, U3.16
ROW14_L: D10.1, D103.1, J1.28, J2.28, U1.15
ROW15_H: J1.29, J2.29, U3.17
ROW15_L: D9.2, D102.1, J1.30, J2.30, U1.7
ROW16_H: J1.31, J2.31, U3.18
ROW16_L: D9.1, D101.1, J1.32, J2.32, R22.2, U1.5
ROW_REG_CLK: U1.12, U2.12, U4.12, U5.12, U11.23, U13.13
ROW_REG_CLK_3v3: U12.12, U13.8
SENSE_EN: R28.2, U11.26
SENSE_EN_3v3: R23.2, R28.1, U12.7
~COL_EN: J4.1, U11.24, U13.14
~COL_EN_3v3: U12.13, U13.7
~RC_CLEAR: J4.5, U1.8, U2.8, U4.8, U5.8, U11.27, U13.18
~RC_CLR_3v3: U12.5, U13.3
~ROW_EN: U1.9, U2.9, U4.9, U5.9, U11.25, U13.12
~ROW_EN_3v3: U12.11, U13.9
~SENSE: R25.2, U8.5, U11.30, U13.17
~SENSE_3v3: U12.4, U13.4

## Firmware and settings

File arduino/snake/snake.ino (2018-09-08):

#include <FlipdotPanel.h>
#include <SPI.h>
#include <Wire.h>
#include "Nunchuk.h"
#include "digits.h"

FlipdotPanel flipdots;


// Joystick actions
#define NONE 0
#define UP 1
#define DOWN 2
#define RIGHT 3
#define LEFT 4

byte rowCount = 16;
byte colCount = 30;


// Scoring
int score1 = 0;
int score2 = 0;
int highScore = 0;
int moveCount;

byte playerCount = 2;
byte activePlayer = 1;

bool invert = false;
bool wrapWall = false;

// Positions occupied by snake. Index 0 is the tail, and
// index snakelen-1 is the head.
const byte MAX_SNAKE = 150;
coord snake[MAX_SNAKE];
byte snakelen = 0;

bool foodstate = false;

const byte MAX_FOOD = 5;
coord food[MAX_FOOD];
byte foodlen = 0;


void setFood(bool state) {

  for (byte n=0;  n<foodlen;  n++) {
    flipdots.setPixel(food[n], state, invert);
  }
}

void setSnake(bool state) {

  for (byte n=0;  n<snakelen;  n++) {
    flipdots.setPixel(snake[n], state, invert);
  }
}

void resetGame() {
  score1 = 0;
  score2 = 0;
  activePlayer = 1;
}

void resetHalfRound(byte player) {

    snakelen = 4;
    if (player == 1) {
      snake[0].X = 5;
      snake[0].Y = 8;
      snake[1].X = 6;
      snake[1].Y = 8;
      snake[2].X = 7;
      snake[2].Y = 8;
      snake[3].X = 8;
      snake[3].Y = 8;
    }
    else {
      snake[0].X = colCount - 6;
      snake[0].Y = 8;
      snake[1].X = colCount - 7;
      snake[1].Y = 8;
      snake[2].X = colCount - 8;
      snake[2].Y = 8;
      snake[3].X = colCount - 9;
      snake[3].Y = 8;
    }
    foodlen = 0;
    addFoodAwayFromSnakeAndFood(12);
    foodstate = false;

    moveCount = 0;
}



byte joystick() {

    if (nunchuk_read()) {

      int8_t X = nunchuk_joystickX();
      int8_t Y = nunchuk_joystickY();

        if (X < -80  &&  X < Y) {
          return LEFT;
        }
        if (X > 80  &&  X > Y) {
          return RIGHT;
        }
        if (Y < -80  &&  Y < X) {
          return DOWN;
        }
        if (Y > 80  &&  Y > X) {
          return UP;
        }
    }

    return NONE;
}

bool buttonZ() {
  return (nunchuk_buttonZ() != 0);
}

bool buttonC() {
  return (nunchuk_buttonC() != 0);
}


void clearPanel() {
  
  for (byte n=0;  n<4;  n++) {
    flipdots.setAllColumns(0b1010101010101010, 0xffff, invert);
    delay(100);
    flipdots.setAllColumns(0b0101010101010101, 0xffff, invert);
    delay(100);
  }
  
  flipdots.setAllColumns(0x0000, 0xffff, invert);
}

void showSnake() {
  for (byte n=0;  n<snakelen;  n++) {
    flipdots.setPixel(snake[n], true, invert);
  }
}

// Move the head of the snake, optionally getting longer.
// Returns 0 if move is OK, or -1 if snake hits self or walls.
// Returns 1 on food eating.
int8_t moveSnake(byte direction, bool enlongen) {

  coord head = snake[snakelen-1];

  if (enlongen && snakelen == MAX_SNAKE) {
    // Cancel enlongen.
    enlongen = false;
  }

  if (!enlongen) {
    // Turn off tail end
    flipdots.setPixel(snake[0], false, invert);

    // Shift snake
    for (byte n=1;  n<snakelen;  n++) {
      snake[n-1] = snake[n];
    }
  }
  else {
    snakelen++;
  }

  switch(direction){
    case UP:
      if (head.Y == 0)
        return -1;
      head.Y = head.Y-1;
      break;
    case DOWN:
      if (head.Y == rowCount-1)
        return -1;
      head.Y = head.Y+1;
      break;
    case LEFT:
      if (head.X == 0)
        return -1;
      head.X = head.X-1;
      break;
    case RIGHT:
      if (head.X == colCount-1)
        return -1;
      head.X = head.X+1;
      break;
  }

  snake[snakelen-1] = head;
  flipdots.setPixel(head, true, invert);

  if (hitSelf()) {
    // Game over.
    return -1;
  }

  if (hitFood()) {
    return 1;
  }

  return 0;
}

// Detect self-crossing snakeness: is head already in rest of body?
bool hitSelf() {

  coord head = snake[snakelen-1];
  for (byte n=0;  n<snakelen-1;  n++) {
    if (head.X == snake[n].X  &&  head.Y == snake[n].Y)
      return true;
  }

  return false;
}

// Returns true if head is over food. Consumes food.
bool hitFood() {
  coord head = snake[snakelen-1];
  for (byte n=0;  n<foodlen;  n++) {
    if (head.X == food[n].X  &&  head.Y == food[n].Y) {
      // Consume food
      if (n < foodlen-1) {
        food[n] = food[foodlen-1];
      }
      foodlen--;
      return true;
    }
  }

  return false;
}

// Wait until a joystick action, then return it.
byte awaitAction() {
  byte action = NONE;

  while(action != UP && action != DOWN && action != LEFT && action != RIGHT) {
    action = joystick();
  }

  return action;
}

// Add more food.
void moarFood() {

  if (foodlen >= MAX_FOOD)
    return;
  addFoodAwayFromSnakeAndFood(6);
}

// Pick a food location at least dist positions away from snake and other food.
// Try up to 20 times, then give up.
void addFoodAwayFromSnakeAndFood(int8_t dist) {

  bool tooClose = false;

  coord f = {};

  for (byte tries=0;  tries<20;  tries++) {
    f.X = random(colCount);
    f.Y = random(rowCount);

    tooClose = false;

    // Compare with snake
    for (byte n=0;  n<snakelen;  n++) {
      if ((f.X > snake[n].X - dist) && (f.X < snake[n].X + dist) && (f.Y > snake[n].Y - dist) && (f.Y < snake[n].Y + dist)) {
        tooClose = true;
        break;
      }
    }

    if (!tooClose) {
      // Compare with food
      for (byte n=0;  n<foodlen;  n++) {
        if ((f.X > food[n].X - dist) && (f.X < food[n].X + dist) && (f.Y > food[n].Y - dist) && (f.Y < food[n].Y + dist)) {
          tooClose = true;
          break;
        }
      }
    }

    if (!tooClose) {
      food[foodlen++] = f;
      return;
    }
  }

  // No dice.
  return;
}

byte limitRightAngles(byte action, byte prevAction) {
      // Limit direction to right angle moves (no backsies)
    switch (action) {
      case UP:
        if (prevAction == DOWN)
          return prevAction;
        break;
      case DOWN:
        if (prevAction == UP)
          return prevAction;
        break;
      case LEFT:
        if (prevAction == RIGHT)
          return prevAction;
        break;
      case RIGHT:
        if (prevAction == LEFT)
          return prevAction;
    }

  return action;
}

void reverseSnake() {

  delay(1500);

  // Animate reversal
  for (byte n=0;  n<snakelen;  n++) {
    flipdots.setPixel(snake[n], false, invert);
    delay(35);
    flipdots.setPixel(snake[n], true, invert);
    delay(35);
  }

  // Reverse snake
  byte halflen = snakelen >> 1;
  for (byte n=0; n<(halflen);  n++) {
    coord temp = snake[n];
    snake[n] = snake[snakelen-1-n];
    snake[snakelen-1-n] = temp;
  }

  // Animate reversed snake
  for (byte n=0;  n<snakelen;  n++) {
    flipdots.setPixel(snake[n], false, invert);
    delay(35);
    flipdots.setPixel(snake[n], true, invert);
    delay(35);
  }
  
  // Determine forbidden direction
  byte idleAction;

  if (snake[snakelen-1].X - snake[snakelen-2].X > 0) {
    idleAction = LEFT;
  }
  if (snake[snakelen-1].X - snake[snakelen-2].X < 0) {
    idleAction = RIGHT;
  }
  if (snake[snakelen-1].Y - snake[snakelen-2].Y > 0) {
    idleAction = UP;
  }
  if (snake[snakelen-1].Y - snake[snakelen-2].Y < 0) {
    idleAction = DOWN;
  }

  while (awaitAction() == idleAction)
    ;
}

// Play a single round, one or two players.
void playHalfRound(byte player) {

  invert = (player == 2);

  showSnake();

  byte action = NONE;
  byte prevAction = NONE;
  byte halfAction = NONE;
  int speedCount = 0;
  int foodCount = 0;
  int moveDelay = 250;
  
  // Wait for non-forbidden action.
  byte idleAction = LEFT;
  if (player == 2)
    idleAction = RIGHT;

  while (awaitAction() == idleAction)
    ;
  int8_t result = 0;
  bool longen = false;

  while (result > -1) {

    // Snake reversal?
    if (buttonC() && buttonZ()) {
      reverseSnake();
      halfAction = joystick();
      prevAction = halfAction;
    }

    // Handle food
    setFood(foodstate);
    foodstate = !foodstate;

    // Read joystick and move snake
    if (halfAction != NONE) {
      action = halfAction;
    }
    else {
      action = joystick();
    }
  
    if (action == NONE) {
      action = prevAction;
    }

    action = limitRightAngles(action, prevAction);

    prevAction = action;
    result = moveSnake(action, longen);
    longen = false;
    if (result == 1) {
      moarFood();
      longen = true;
    }

    moveCount++;
    speedCount++;
    foodCount++;
    if (speedCount > 120) {
      speedCount = 0;
      if (moveDelay > 50) {
        moveDelay -= 20;
      }
    }
    if (foodCount > 100) {
      foodCount = 0;
      moarFood();
    }

    // Half delay
    delay(moveDelay >> 1);

    // Check joystick between ticks for better gameplay
    halfAction = joystick();

    // Other half of delay.
    delay(moveDelay >> 1);
  }
}

// Play a full game.
void playGame() {
  Serial.println("\n\nPlay snake!");

  for (byte r=1;  r<=3;  r++) {
    Serial.print("Round ");
    Serial.println(r);

    invert = false;
    resetHalfRound(1);
    clearPanel();
    playHalfRound(1);
    setFood(false);
    scoreRound(1);
    delay(5000);
    Serial.print("  Player 1 score: ");
    Serial.println(score1);
    
    if (playerCount == 2) {
      invert = true;
      resetHalfRound(2);
      clearPanel();
      playHalfRound(2);
      setFood(false);
      scoreRound(2);
      delay(5000);
      Serial.print("  Player 2 score: ");
      Serial.println(score2);
    }
  }
}

void displayDigit(byte d, byte row, byte col, uint16_t mask) {
  uint16_t colbits = 0;

  for (byte i=0;  i<4;  i++) {
    colbits = digit_table[d][i] << row;
    flipdots.setColumn(col, colbits, mask, invert);

    col--;
  }
}

void displayScore(int score, byte row, byte col, uint16_t mask) {

  if (score == 0) {
    displayDigit(0, row, col, mask);
  }
  while (score > 0 ) {
    byte n = score % 10;
    displayDigit(n, row, col, mask);

    col -= 5;
    score /= 10;
  }
}

void showCurrentScoreSplit() {

  invert = false;
  flipdots.setAllColumns(0xff00);
  displayScore(score1, 0, 25, 0x00ff);
  invert = true;
  displayScore(score2, 9, 25, 0xff00);
}

void scoreRound(byte player) {

  for (byte n=0;  n<8;  n++) {
    setSnake(false);
    delay(20);
    setSnake(true);
    delay(20);
  }
  delay(1500);

  // Dissolve snake pixel by pixel
  for (byte n=0;  n<snakelen;  n++) {
    flipdots.setPixel(snake[n], false, invert);
    delay(125);
  }

  showCurrentScoreSplit();
  delay(1500);
  byte w = 50;
  int points = snakelen * 25;
  if (player == 1) {
    invert = false;
    int newscore = score1 + points;
    while (score1 < newscore) {
      if (w > 20)
        score1++;
      else {
        score1 += 5;
        if (score1 > newscore)
          score1 = newscore;
      }
      displayScore(score1, 0, 25, 0x00ff);
      delay(w);
      if (w > 4)
        w--;
    }
  }
  else {
    invert = true;
    int newscore = score2 + points;
    while (score2 < newscore) {
      if (w > 20)
        score2++;
      else {
        score2 += 5;
        if (score2 > newscore)
          score2 = newscore;
      }
      displayScore(score2, 9, 25, 0xff00);
      delay(w);
      if (w > 4)
        w--;
    }
  }
}

void showScores() {
  Serial.println("Scores: ");
  Serial.print("  Player 1: ");
  Serial.println(score1);
  Serial.print("  Player 2: ");
  Serial.println(score2);

  if (score1 > highScore) {
    highScore = score1;
  }
  if (score2 > highScore) {
    highScore = score2;
  }

  Serial.print("High score: ");
  Serial.println(highScore);
}

void setup() {

	Serial.begin(115200);
	flipdots.begin();
	SPI.begin();

	Serial.print("No. of panels: ");
	Serial.println(flipdots.panelCount);

	Serial.print("No. of columns: ");
	Serial.println(flipdots.columnCount);

  colCount = flipdots.columnCount;

	flipdots.setAllColumns(0x0000);

  Wire.begin();
  nunchuk_init_power(); // A1 and A2 is power supply
  nunchuk_init();
  randomSeed(analogRead(0));
}

void loop() {
  resetGame();
  playGame();
  showScores();
}

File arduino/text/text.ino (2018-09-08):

#include <FlipdotPanel.h>
#include <SPI.h>
#include "ascii.h"

FlipdotPanel flipdots;

// Dynamically sized in setup
uint16_t *columns = 0;
byte columnCount = 0;

void shift() {
	for (byte n=0;  n<columnCount-1;  n++) {
		columns[n] = columns[n+1];
	}
	columns[columnCount-1] = 0;
}

void write() {
	for (byte n=0;  n<=columnCount-1;  n++) {
		flipdots.setColumn(n, columns[n]);
	}
}

void clear() {
	for (byte n=0;  n<columnCount-1;  n++) {
		columns[n] = 0x0000;
	}
}

void display(char text[], byte top) {

	int len = strlen(text);

	for (int n=0;  n<len;  n++) {
		byte c = text[n] - 32;
		for (byte i=0;  i<5;  i++) {
			int index = c*5 + i;
			uint16_t data = Font5x7[index] << top;
			shift();
			columns[columnCount-1] = data;
			write();
		}
		shift();
		columns[columnCount-1] = 0;
		write();
	}
}

char hello[] = "Hello";
char thanks[] = "Thanks for watching!  ";
char watch[] = "Watch ";
char appeal[] = "Please LIKE and SUBSCRIBE";

char flipmaster[] = "FlipMaster 9000  "; 
char part1[] = "Part 1  ";
char part2[] = "Part 2  ";
char part3[] = "Part 3  ";
char part4[] = "Part 4  ";
char part5[] = "Part 5  ";

void setup() {
	Serial.begin(115200);
	flipdots.begin();
	SPI.begin();

	Serial.print("No. of panels: ");
	Serial.println(flipdots.panelCount);

	Serial.print("No. of columns: ");
	Serial.println(flipdots.columnCount);
	
	columnCount = flipdots.columnCount;
	columns = new uint16_t[columnCount];
	for (byte i=0;  i<columnCount;  i++) {
		columns[i] = 0;
	}

	flipdots.setAllColumns(0x0000);
	delay(2000);

	display(hello, 5);

	delay(5000);

	display(thanks, 0);
	display(watch, 8);
	display(part2, 8);
	display(appeal, 5);
	delay(500);

	for (byte i=0;  i<3;  i++) {
		flipdots.setAllColumns(0x0000);
		delay(250);
		write();
		delay(250);
	}

	delay(2000);
	clear();
	write();
	delay(2000);

	display(thanks, 0);
	display(watch, 8);
	display(part3, 8);
	display(appeal, 5);
	delay(500);

	for (byte i=0;  i<3;  i++) {
		flipdots.setAllColumns(0x0000);
		delay(250);
		write();
		delay(250);
	}

	delay(2000);
	clear();
	write();
	delay(2000);

	display(thanks, 0);
	display(watch, 8);
	display(part4, 8);
	display(appeal, 5);
	delay(500);

	for (byte i=0;  i<3;  i++) {
		flipdots.setAllColumns(0x0000);
		delay(250);
		write();
		delay(250);
	}

	delay(2000);
	clear();
	write();
	delay(2000);

	display(thanks, 0);
	display(watch, 8);
	display(part5, 8);
	display(appeal, 5);
	delay(500);

	for (byte i=0;  i<3;  i++) {
		flipdots.setAllColumns(0x0000);
		delay(250);
		write();
		delay(250);
	}

	delay(2000);
	clear();
	write();
	delay(2000);

	display(thanks, 0);
	display(appeal, 5);
	delay(500);

	for (byte i=0;  i<3;  i++) {
		flipdots.setAllColumns(0x0000);
		delay(250);
		write();
		delay(250);
	}

	delay(2000);
	clear();
	write();
	delay(2000);


	display(flipmaster, 5);
	display(part1, 5);

	delay(2000);
	clear();
	write();
	delay(2000);

	display(flipmaster, 5);
	display(part2, 5);

	delay(2000);
	clear();
	write();
	delay(2000);

	display(flipmaster, 5);
	display(part3, 5);

	delay(2000);
	clear();
	write();
	delay(2000);

	display(flipmaster, 5);
	display(part4, 5);
	
	delay(2000);
	clear();
	write();
	delay(2000);

	display(flipmaster, 5);
	display(part5, 5);
	delay(2000);
	clear();
	write();

}

void loop() {
}

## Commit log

2018-05-16 Pass DRC on row driver schematic
    [row_driver.sch]
2018-05-16 Add footprints
    [row_driver.sch]
2018-05-17 More footprint selection
    [row_driver.sch]
2018-05-18 Cleanup; add test points; add column line pullup/pulldowns
    [row_driver.sch]
2018-05-19 Row board nearly done; added test points
    [row_driver.sch]
2018-05-20 Add column board
    [column_driver.kicad_pcb, column_driver.sch]
2018-05-21 Finish column board schematic
    [column_driver.sch]
2018-05-21 Starting row board layout
    [column_driver.sch, row_driver.kicad_pcb, row_driver.sch]
2018-05-21 Replace BAV23 with BAS16GW
    [row_driver.kicad_pcb, row_driver.sch]
2018-05-26 Begin layout
    [row_driver.kicad_pcb, row_driver.sch]
2018-05-30 Add reverse power protection; data sheets
    [row_driver.kicad_pcb, row_driver.sch]
2018-06-01 Prior to deleting ESP8266
    [row_driver.sch]
2018-06-08 Combine two controllers
    [row_driver-B.Cu.dxf, row_driver-B.Mask.dxf, row_driver-B.SilkS.dxf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]
2018-06-10 Routed shift registers and row connectors
    [row_driver.kicad_pcb, row_driver.sch]
2018-06-11 Routed all but controllers
    [row_driver.kicad_pcb, row_driver.sch]
2018-06-15 Finished routing row board; cleaning up.
    [row_driver-B.Cu.dxf, row_driver-B.Mask.dxf, row_driver-F.Cu.dxf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]
2018-06-15 Fully routed row board
    [row_driver.kicad_pcb]
2018-06-22 Mostly routed column board
    [column_driver.kicad_pcb, column_driver.sch, row_driver-B.Cu.dxf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]
2018-06-22 Nearly done routing column board.
    [column_driver.kicad_pcb]
2018-06-22 All connections routed. Board still ugly.
    [column_driver.kicad_pcb]
2018-06-23 Parts positioned
    [column_driver.kicad_pcb]
2018-06-24 About to move high side drivers
    [column_driver.kicad_pcb]
2018-06-25 Final routing
    [column_driver.kicad_pcb]
2018-06-26 Fully routed column board
    [column_driver.kicad_pcb]
2018-06-26 Cleanup on column board
    [column_driver.kicad_pcb]
2018-06-26 Update column board
    [column_driver.kicad_pcb]
2018-06-27 Add Gerber and DXF files for row and column boards
    [column_driver-B.Cu.dxf, column_driver-B.Mask.dxf, column_driver-B.SilkS.dxf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]
2018-07-01 Add project-local footprints and 3D models
    [C_0805.step, LED_D3.0mm.FCStd, R_0805.step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]
2018-07-01 Localize footprints and 3D models in column board; add images
    [column_driver.kicad_pcb, column_driver.sch]
2018-07-01 Remove row_driver-rescue library from row driver schematic
    [row_driver.sch]
2018-07-18 Clean up flipColOn and flipColOff
    [nano_test.ino]
2018-08-06 Add snake reversal feature
    [snake.ino]
2018-08-27 Created FlipdotPanel library to abstract away the controller.
    [text.ino]
2018-08-28 Update snake.ino to use FlipdotPanel library.
    [snake.ino]
2018-09-08 Update Snake to use FlipdotPanel library.
    [nano_test.ino, random.ino, snake.ino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]

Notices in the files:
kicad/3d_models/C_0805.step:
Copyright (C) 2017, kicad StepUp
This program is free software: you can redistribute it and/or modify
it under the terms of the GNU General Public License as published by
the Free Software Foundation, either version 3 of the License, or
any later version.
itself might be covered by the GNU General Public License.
